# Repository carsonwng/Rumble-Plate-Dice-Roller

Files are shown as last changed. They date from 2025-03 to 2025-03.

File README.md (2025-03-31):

# Rumble Plate Dice Roller
This project is an adapted version of the V2 Rumble Plate Dice Roller published by MMC. It was produced by a Queen's Engineering APSC 103 group, team 854-A. It's goals are to improve upon the original design, reducing noise, improving ergonomics, and improving reliability. 

A switch adapted device to roll the dice for any game night!

This switch activated dice roller utilizes a hobby motor, battery holder, Omron switch, and 3.5mm jack along with a couple 3d printed parts and a clear plastic cup to make any dice game more accessible. This device is a new development of the Dice Spinner that features faster dice rolling and variations in allowable cup size.

The Rumble Plate Dice Roller allows for approximately 10oz to 22oz clear plastic cups. Following the assembly guide, the components can be wired and mounted, then the dice roller is all ready to use! It is an easy toy to make that allows people to roll the dice in an alternative way.

# Usage

An AT switch can be plugged into the 3.5mm jack on the side of the device to be used for activation. Alternatively, the on-device switch can be used for activation. The on-device button would be meant more for others playing around the table who are able to reach over and wrap their hands around the base to push the button. With the additional print of the vertical push base, the on-device button can be used to turn the device itself into the activation button such that anyone around the table can push on to top of  the clear cup to roll the dice. This on-device button can be used in tandem with the corded AT switch.

# Required Skills:

 - Soldering
 - 3D Printing

# Required Components

 - Motor
 - AA Battery Holder
 - Velcro
 - Abra Switch
 - 3.5mm Jack
 - Clear Plastic Cup
 - Dice
 - 3D Printed Parts

# Printing Instructions

- Print the STL files in their given orientations
- 0.3 mm Layer height
- No supports
- No brim

# Build Instructions

This device consists of several 3D printed components and electrical components that assemble together and can be used in tandem with an assistive switch. All STL’s and documentation can be found in the downloadable maker files in the GitHub Repository.

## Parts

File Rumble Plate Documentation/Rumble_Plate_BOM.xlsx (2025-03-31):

Device: Rumble Plate Dice Tumbler |  |  |  |  |  | Total Cost | Total Print time (hr) | Total filament (g)
Version: V3.0 | Date Created: 9/14/2021 |  |  |  |  | $13.46 | 3.67 | 119.13
Commercial Parts:
Part type (Electrical. Mechanical, Sanitization, ect) | Part | Quantity Needed | Pkg Quantity | Price per package | Price per Unit | Price for qty needed |  | Link
Electrical | DC Motor | 1 | 1 | $2.35 | $2.35 | $2.35 |  | https://www.digikey.ca/en/products/detail/adafruit-industries-llc/711/5353610
Electrical | 3.5mm Mono Jack | 1 | 1 | $1.60 | $1.60 | $1.60 |  | https://www.digikey.ca/short/pq1d1z
Electrical | Switch (Abra PBS-DS500-NO-RD) | 1 | 1 | $0.85 | $0.85 | $0.85 |  | https://www.digikey.ca/short/jvzq2d
Electrical | AA Battery Holder | 1 | 1 | $1.26 | $1.26 | $1.26 |  | 2271 Kitronik Ltd. | Battery Products | DigiKey (https://www.digikey.ca/en/products/detail/kitronik-ltd/2271/8635436?productid=8635436)
Mechanical | Cup | 1 | 50 | $4.47 | $0.09 | $0.09 |  | https://www.walmart.ca/en/ip/great-value-plastic-party-cups-clear/6000198044907
Mechanical | Dice | 2 | 5 | $5.00 | $1.00 | $2.00 |  | https://www.walmart.ca/en/ip/ACE-Dice-5ct/PRD54IXGNXVYTJP
Electrical | AA Batteries | 2 | 12 | $13.98 | $1.17 | $2.33 |  | https://www.walmart.ca/en/ip/energizer-max-alkaline-aaa-batteries-2-pack/PRD3IIHXYVK66QB
3D Printed Parts ESTIMATED PRICING USING 1KG ROLL COST: | $25.00
Part (estimated with 0.3 mm layer height) | Description | Quantity Needed | TOTAL Mass (g) | Estimated Price | Print Time (Min) | Link
Base | 3D printed Part | 1 | 77.46 | $1.94 | 124
Cam | 3D printed Part | 1 | 1.64 | $0.04 | 5
Plate | 3D printed Part | 1 | 21.26 | $0.53 | 40
Lid | 3D printed Part | 1 | 18.77 | $0.47 | 51
 |  |  | Total Print Cost: | $2.98
Tools for Assembly
Soldering Iron
Pliers
Wire Cutters
Wire Strippers
Sharp Knife
Alternatives (if there are other sources for some parts link them below)
Part and description | Link
Cups | Free from a coffee shop/restaurant
DC Motor | Brushed DC Motor 2 (RM2) - RobotShop (https://www.robotshop.com/ca/en/solarbotics-regular-motor-2.html)
DC Motor (Bulk) | https://www.amazon.ca/Gikfun-Motor-Electric-Arduino-EK1291x10C/dp/B06WLL6QM5?hvadid=292968375828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

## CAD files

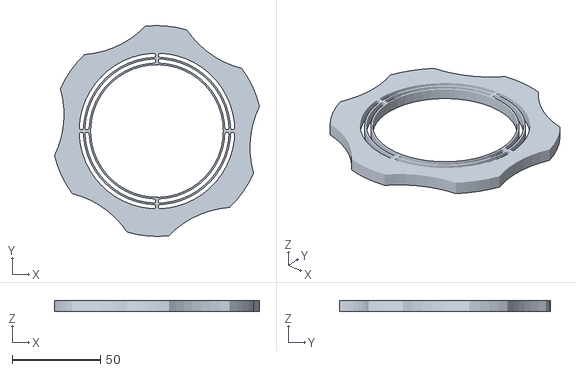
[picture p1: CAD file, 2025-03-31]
Rumble Plate STLs/RedesignedLid.STL
115.9 x 119.2 x 6.50

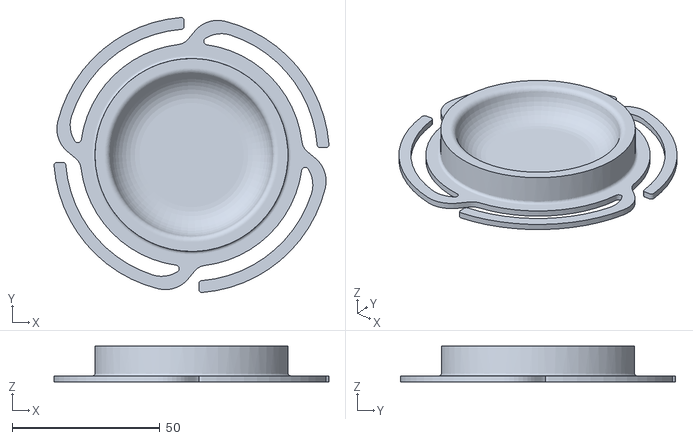
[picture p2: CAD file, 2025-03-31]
Rumble Plate STLs/RedesignedFlexPlate.STL
92.9 x 92.9 x 12.0

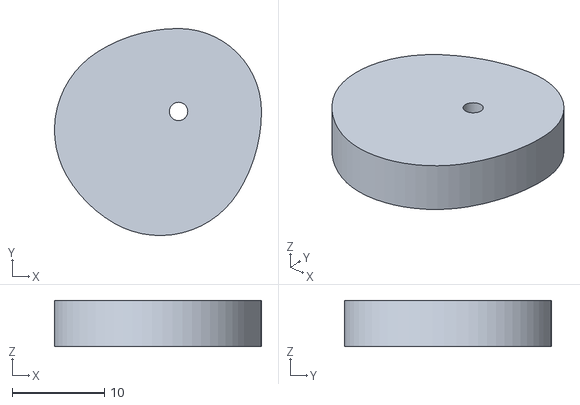
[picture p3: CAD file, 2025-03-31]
Rumble Plate STLs/RedesignedCam.STL
22.5 x 22.5 x 5.00

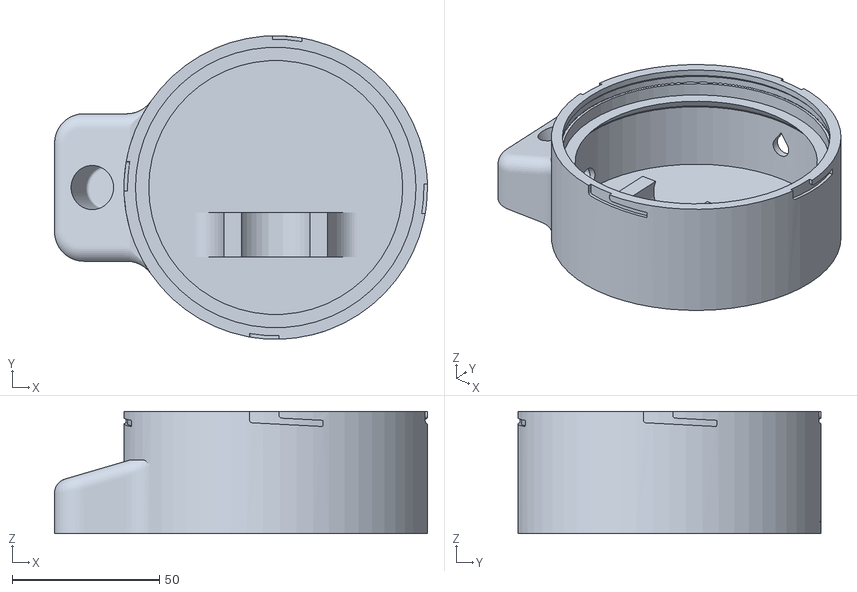
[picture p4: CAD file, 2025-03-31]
Rumble Plate STLs/RedesignedBase.STL
126.5 x 102.9 x 41.5

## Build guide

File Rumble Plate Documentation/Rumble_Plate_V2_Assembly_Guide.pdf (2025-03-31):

V3.0 | March 2025 | APSC 103 Team 854-A

## Rumble Plate Assembly Guide

## Required Components

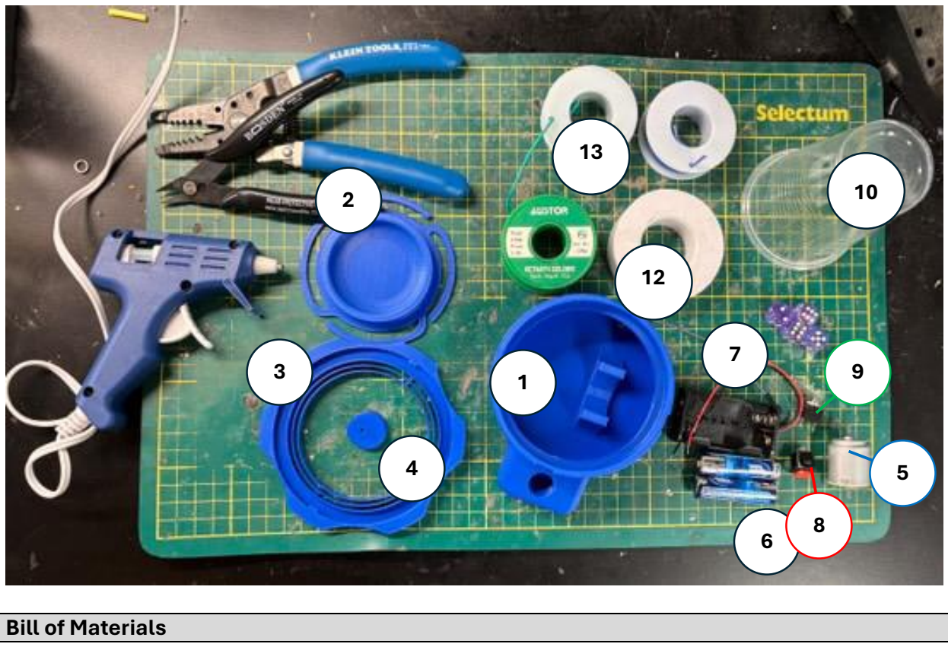
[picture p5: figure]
Bill of Materials

1. 3D Printed Base
2. 3D Printed Plate
3. 3D Printed Lid
4. 3D Printed Cam
5. 29DM9V-DS Double
Shaft DC Motor
6. 2 x AA Batteries
7. AA Battery Holder
8. 14mm Snap-in Round
Push Button
9. 3.5mm Jack
10.Clear Plastic Cup
11. Velcro Patches*
12. Self-Adhesive Foam
(or more Velcro)
13. Wire
14.Dice

Materials marked with * are missing from the diagram above. Required Tools / Supplies

A. Super Glue (and/or Hot Glue)
B. 3D Printer
C. Soldering Iron
D. Wire Cutters
E. Pliers
F. Extra Wire
G. Solder
H. Knife

Required Personal Protective Equipment (PPE)

1. Safety Glasses

## Rumble Plate Assembly Guide Step 1 of 9 – Setting up for Printing

To print the required 3D printed parts, open each of the STL files in the “Rumble Plate STL” folder in PrusaSlicer. If oriented correctly, the parts can all fit appropriately on a Prusa i3 MK3 print bed.

## Step 2 of 9 – Fitting the Cam to the Motor

Using Super Glue or Hot Glue, fix the 3D printed cam to the end of the DC motor – this may be difficult, and may require lots of force to bring the two parts together.
Ensure that you are only Super/hot glueing the 3D printed part, then bringing the axle of the DC motor to that part. Try to keep the glue away from the DC motor as much as possible.

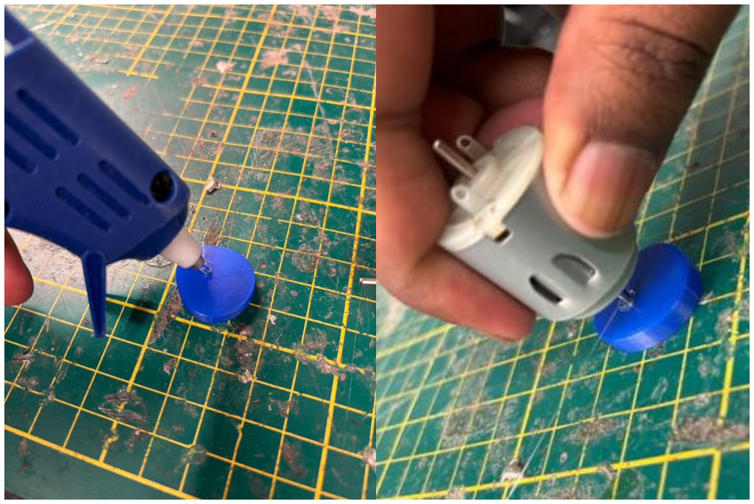
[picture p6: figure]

## Rumble Plate Assembly Guide Step 3 of 9 – Soldering the Button

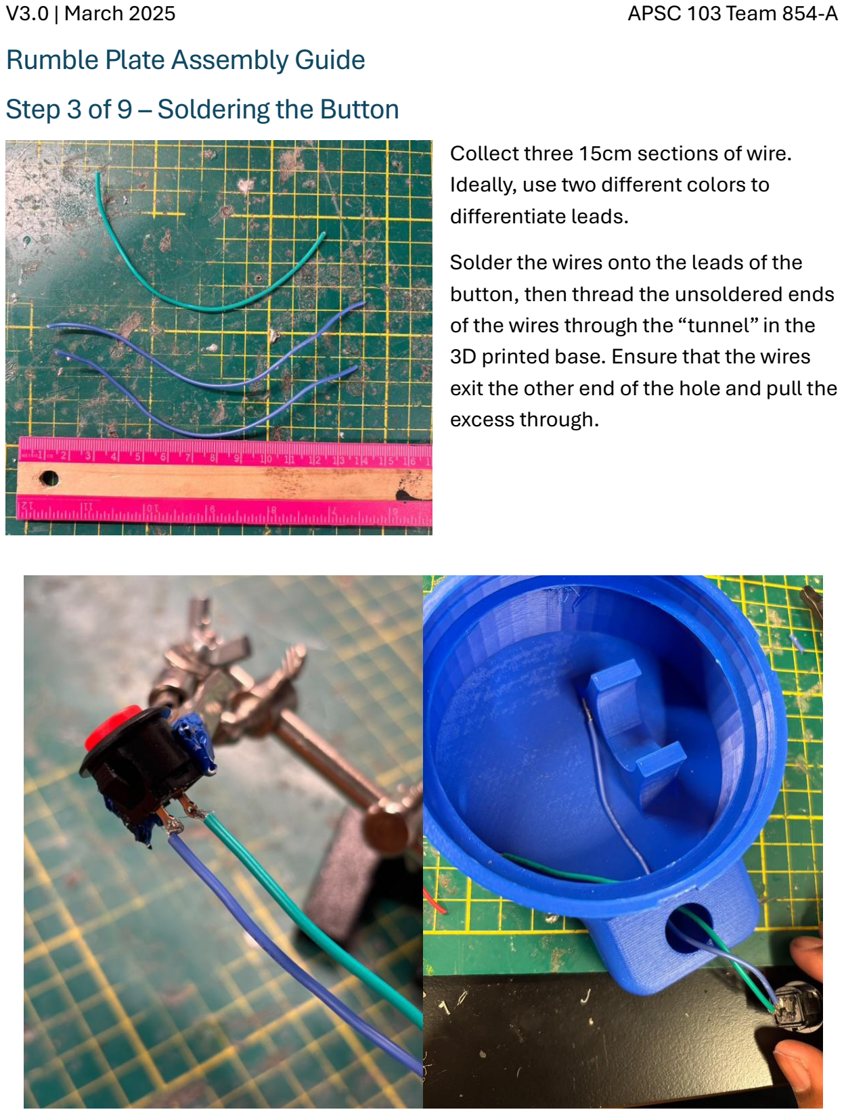
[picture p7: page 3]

Collect three 15cm sections of wire. Ideally, use two different colors to differentiate leads.
Solder the wires onto the leads of the button, then thread the unsoldered ends of the wires through the “tunnel” in the 3D printed base. Ensure that the wires exit the other end of the hole and pull the excess through.

## Rumble Plate Assembly Guide

Press the button into place until you hear a “click”. This is what it should look like when the button is soldered and fixed in place.

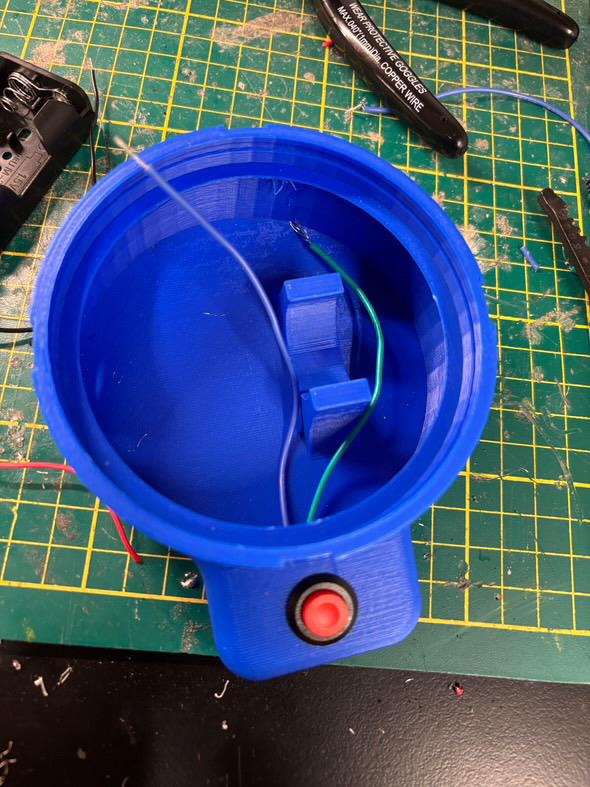
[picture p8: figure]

## Step 4 of 9 – Soldering the 3.5mm Jack

Twist one leading wire from the button with one leading wire from the battery holder.

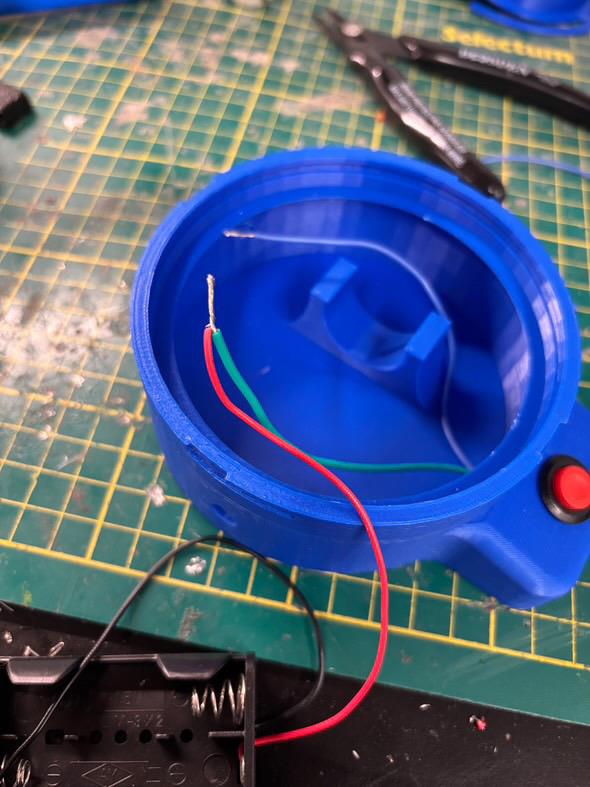
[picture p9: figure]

## Rumble Plate Assembly Guide

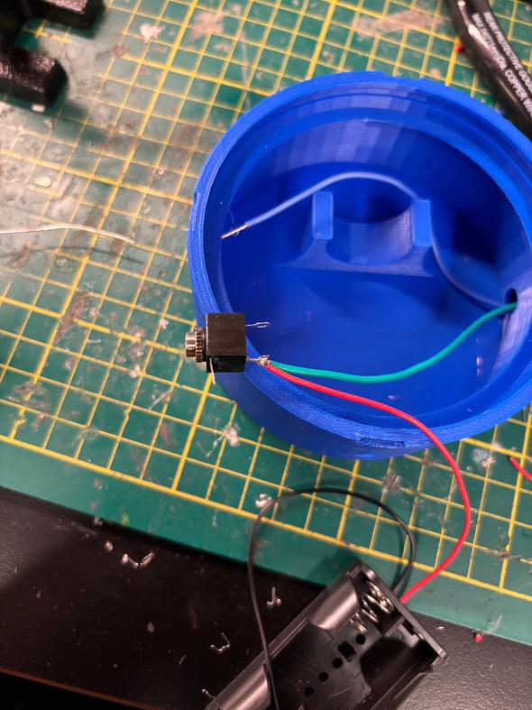
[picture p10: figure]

Solder these twisted wires with one lead from the 3.5mm jack.

## Rumble Plate Assembly Guide

Take the third 15cm section of wire and twist it with the remaining leading wire from the button. Take the untwisted end of this new wire and solder it to the other lead on the 3.5mm jack.

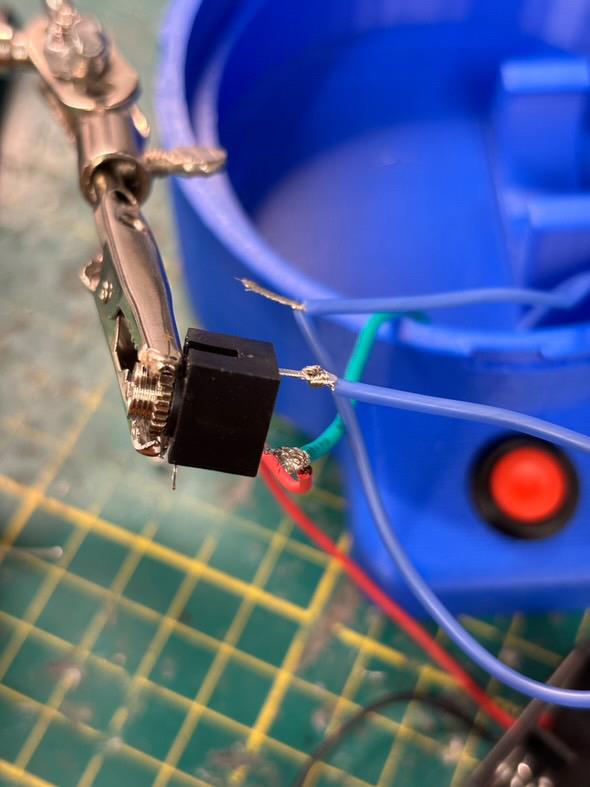
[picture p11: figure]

## Rumble Plate Assembly Guide

## Step 5 of 9 – Soldering the DC Motor

Take the twisted pair of wires from the previous step and solder them on one of the motor’s leads. Be careful not to drop debris or drip solder into the motor itself. Solder the remaining leading wire from the battery case with the second motor lead.

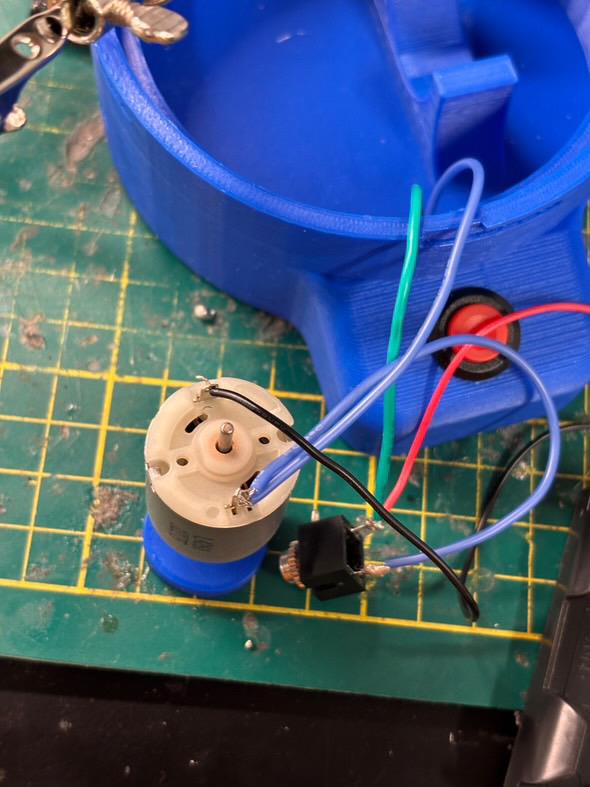
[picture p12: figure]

## Rumble Plate Assembly Guide

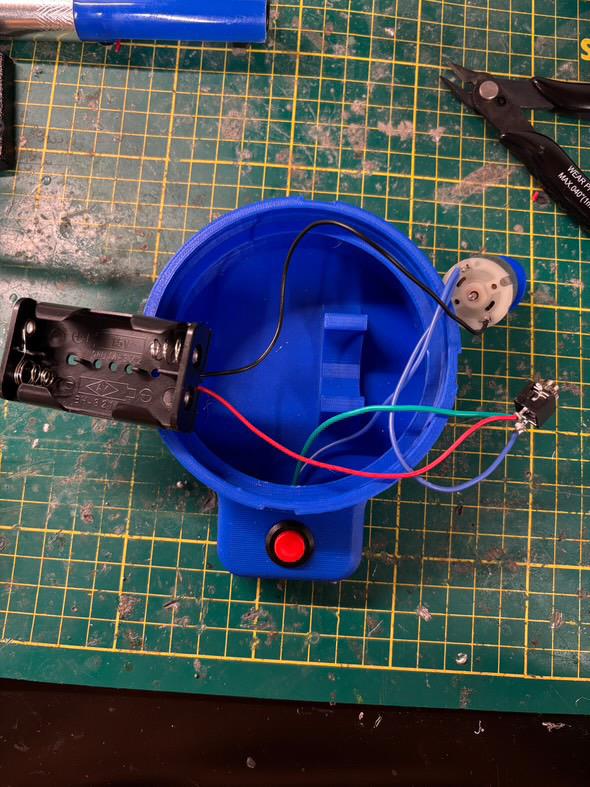
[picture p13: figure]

This is what all of the electronic components should look like when soldered.

## Rumble Plate Assembly Guide

## Step 6 of 9 – Installing the Hardware

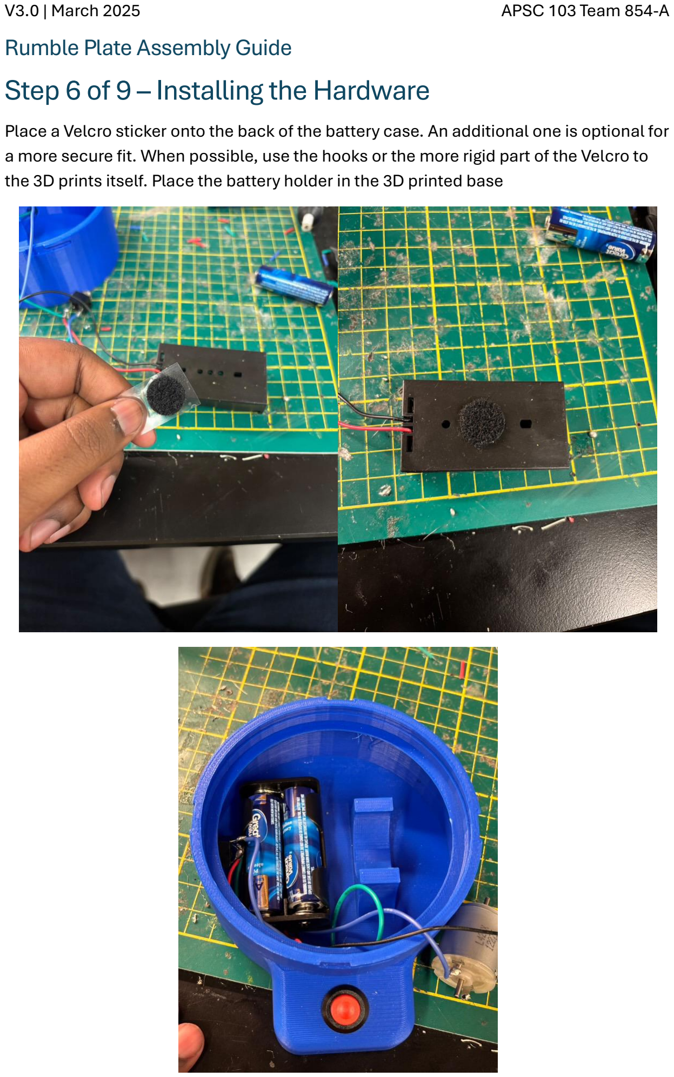
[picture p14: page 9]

Place a Velcro sticker onto the back of the battery case. An additional one is optional for a more secure fit. When possible, use the hooks or the more rigid part of the Velcro to the 3D prints itself. Place the battery holder in the 3D printed base

## Rumble Plate Assembly Guide

## Step 7 of 9 – Installing the 3.5mm Jack

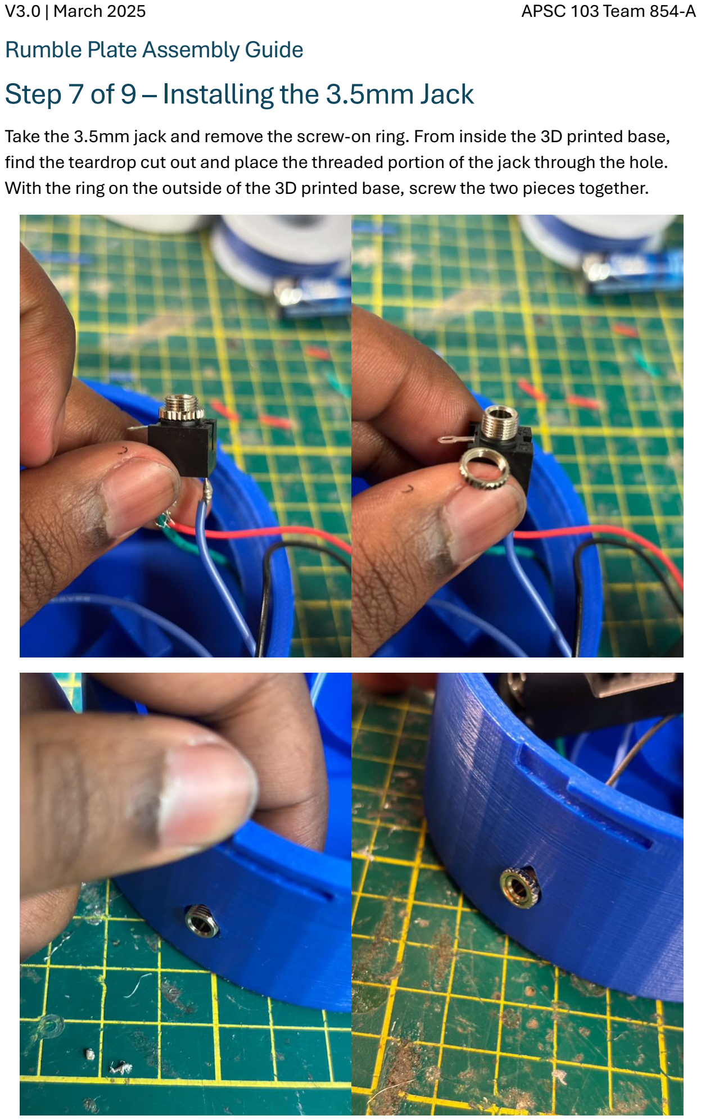
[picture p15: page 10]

Take the 3.5mm jack and remove the screw-on ring. From inside the 3D printed base, find the teardrop cut out and place the threaded portion of the jack through the hole. With the ring on the outside of the 3D printed base, screw the two pieces together.

## Rumble Plate Assembly Guide

## Step 8 of 9 – Installing the DC Motor

Using the self-adhesive foam tape or the soft half of Velcro patches, cut out a 3cm portion and line the fitting for the DC motor. If using self-adhesive foam tape or other double-sided adhesives, be sure to peel the film off before installing the motor.

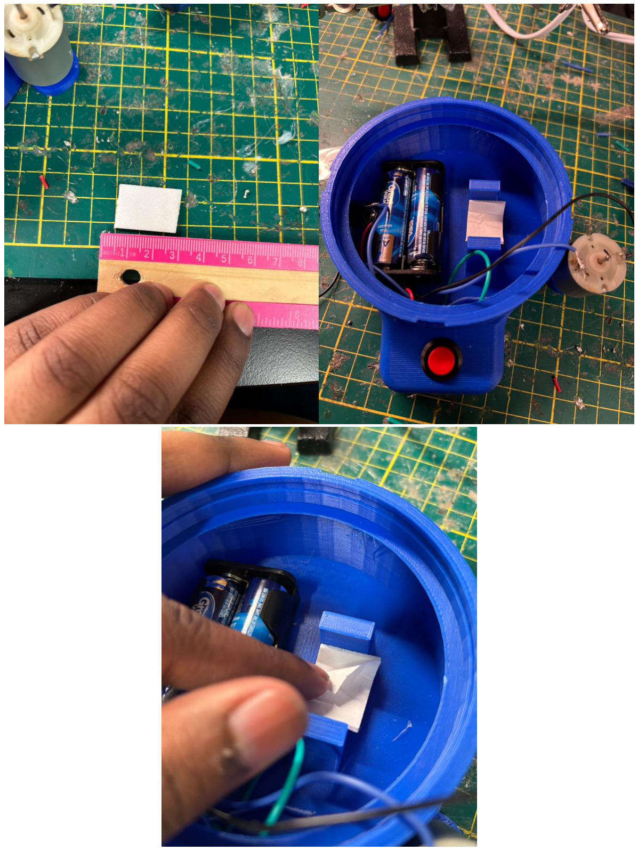
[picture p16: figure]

## Rumble Plate Assembly Guide

Slide the motor into the fitting and press firmly to ensure the adhesives are set properly. Be sure to check that the cam is not touching the battery holder, floor of the 3D printed base, or the fitting for the motor. Adjust as necessary.

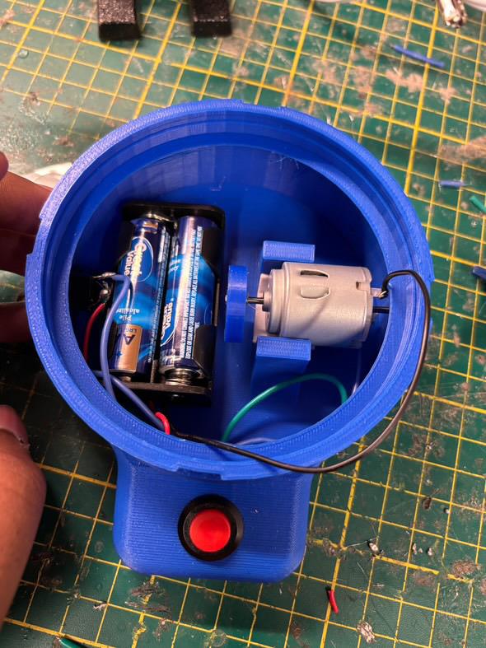
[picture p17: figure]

## Rumble Plate Assembly Guide

## Step 9 of 9 – Putting it all Together

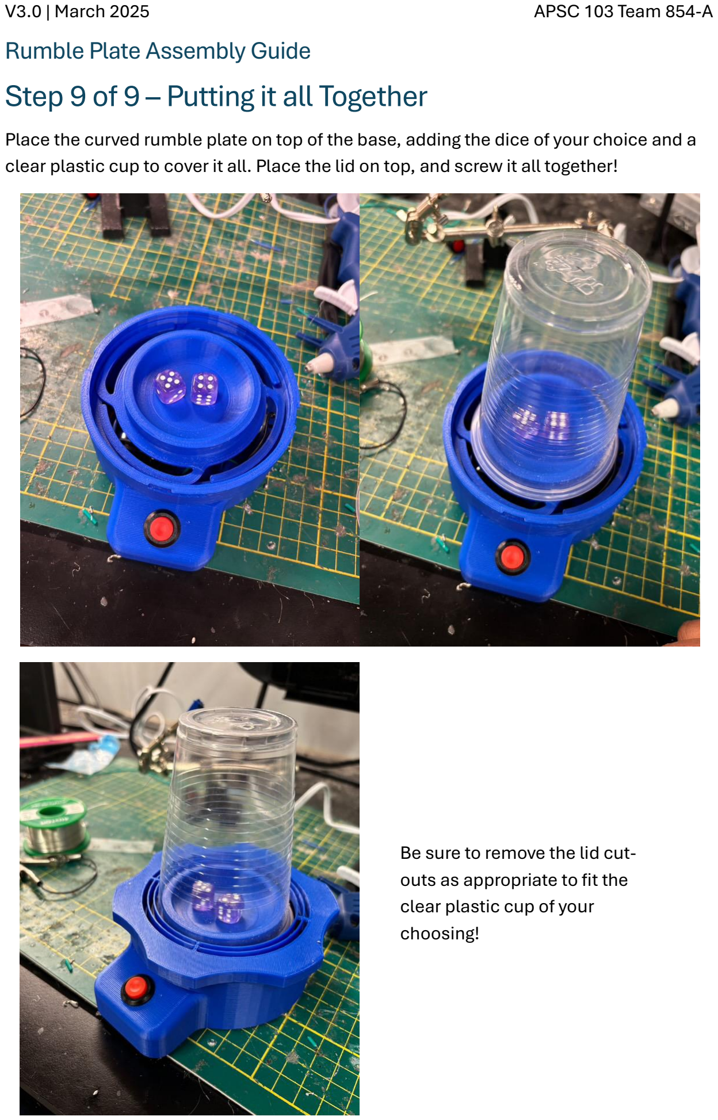
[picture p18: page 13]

Place the curved rumble plate on top of the base, adding the dice of your choice and a clear plastic cup to cover it all. Place the lid on top, and screw it all together!

Be sure to remove the lid cut-outs as appropriate to fit the clear plastic cup of your
choosing!
